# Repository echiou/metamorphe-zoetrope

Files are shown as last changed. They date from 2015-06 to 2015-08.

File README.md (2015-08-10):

# MetaMorphe Zoetrope #
#### By: [Tim Campbell](http://github.com/timcam) and [Ethan Chiou](http://github.com/echiou) ####

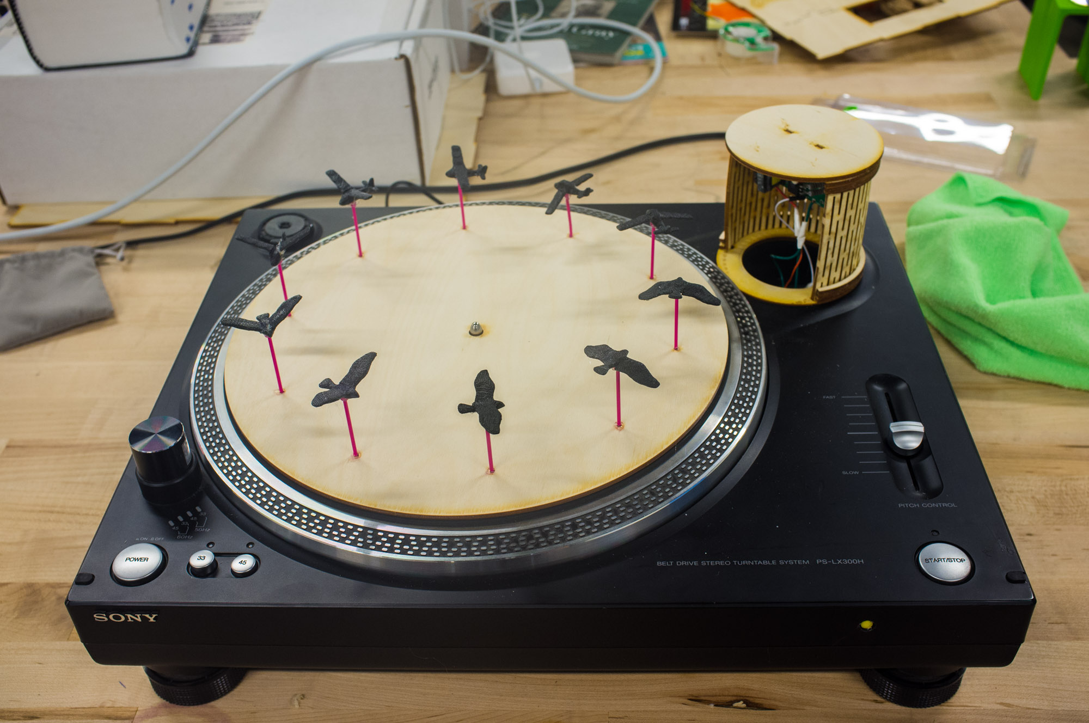
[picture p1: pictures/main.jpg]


A record player modified to demonstrate an application of [Cesar Torres](http://github.com/cearto)' MetaMorphe, namely the ability to interpolate keyframes from a programatically defined change in a 3D model. The record player, which rotates at around three times its built-in speeds (~99 and 135, instead of 33 and 45 rpm, respectively), has either 15 or 10 3D printed models placed on the turntable, and a xenon flash is fired at a corresponding rate to produce the illusion of animation.

A video can be found [here](https://youtu.be/nmKtfB-Ih18).

## How To Run It ##
- Press power button to turn record player on.
- Ensure the strobe off before proceeding
- Select appropriate speed:
    - "33" for 15 frame animations.
    - "45" for 10 frame animations.
- Place an appropriate plate on the turntable.
- Accelerate the turntable using the start/stop button.
    - Ensure the turntable reaches full speed before turning on the strobe.
- Turn on the strobe with the yellow button on the side of the case.
- Tune the speed of the animation with the pitch fader
- When you are done using the zoetrope:
	- Turn off the strobe
	- Turn off the turntable
	- Turn off power

#### Notes ####

- .svg files for [10](./record-10.svg) and [15](./record-15.svg) frame plates can be found in the repository.
- .stl file for the [cog](./stroboscope-cog-rev1.STL) is found in the repository
- .dxf files for the strobe enclosure found in the [strobe-mount](./strobe-mount) folder in the repository
- The turntable must reach full speed before you turn on the strobe because  firing the strobe light and accelerating the turntable simultaneously draws too much power.

## How We Made It ##
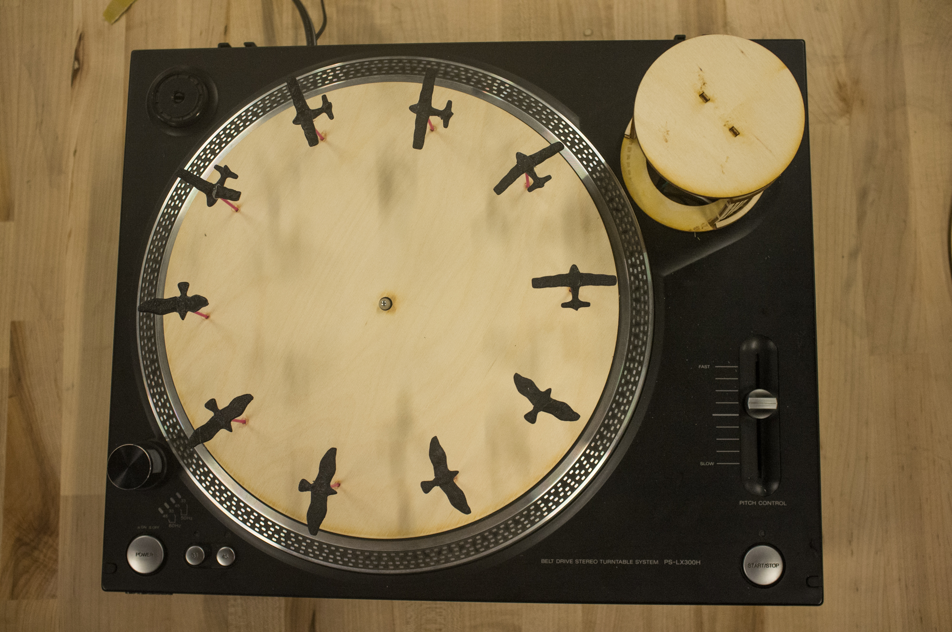
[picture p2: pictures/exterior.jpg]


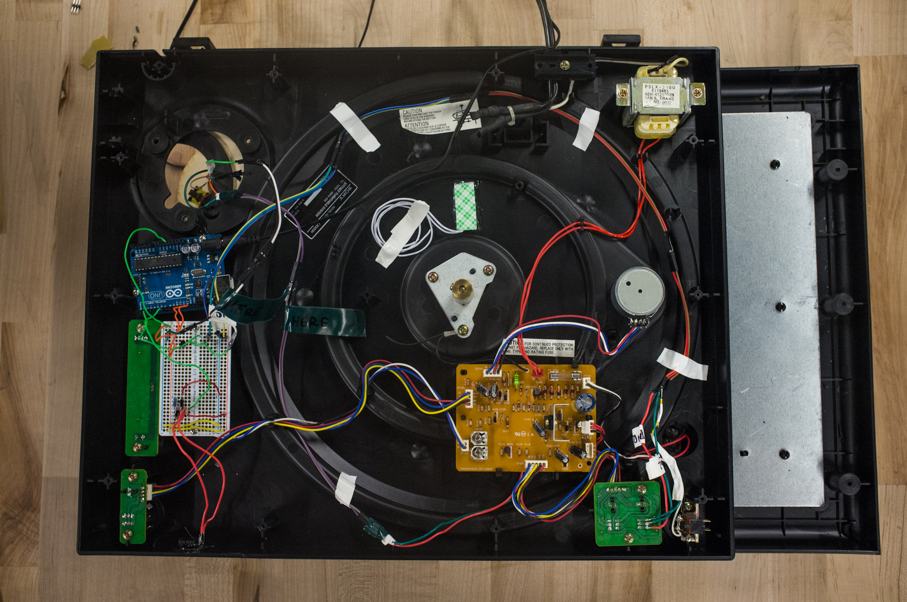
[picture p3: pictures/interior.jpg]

#### 1. [What we started with](#what-we-started-with)
#### 2. [Cog](#cog)
#### 3. [Flash](#flash)
#### 4. [Speed Control](#speed-control)
#### 5. [Circuitry and Programming](#circuitry-and-programming)

## What we started with ##
When approached by Cesar to make a demonstration for MetaMorphe, Tim had the idea of making a zoetrobe or stroboscope to present the potential of MetaMorphe to produce keyframes in animation. We decided on a record player because of the already-implemented rotational motion and the size of the turntable. 
We found an inexpensive, used record player on Craigslist that I picked up in Oakland, and took it apart to see how it worked, and how we could modify it to do what we wanted.

#### Built-In Buttons ####
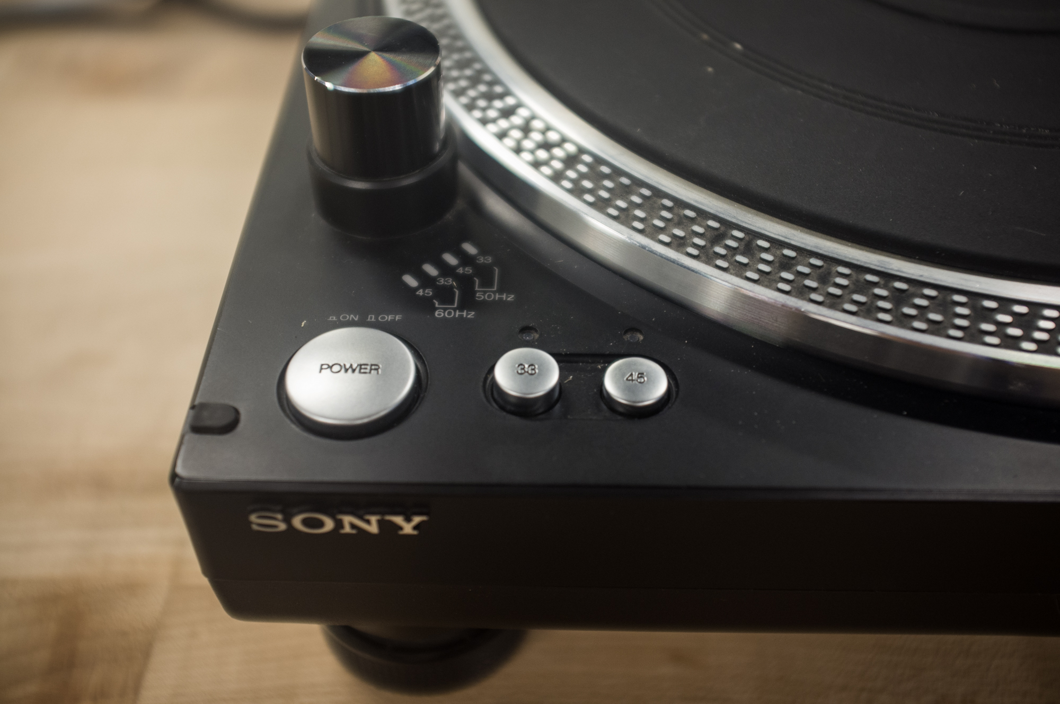
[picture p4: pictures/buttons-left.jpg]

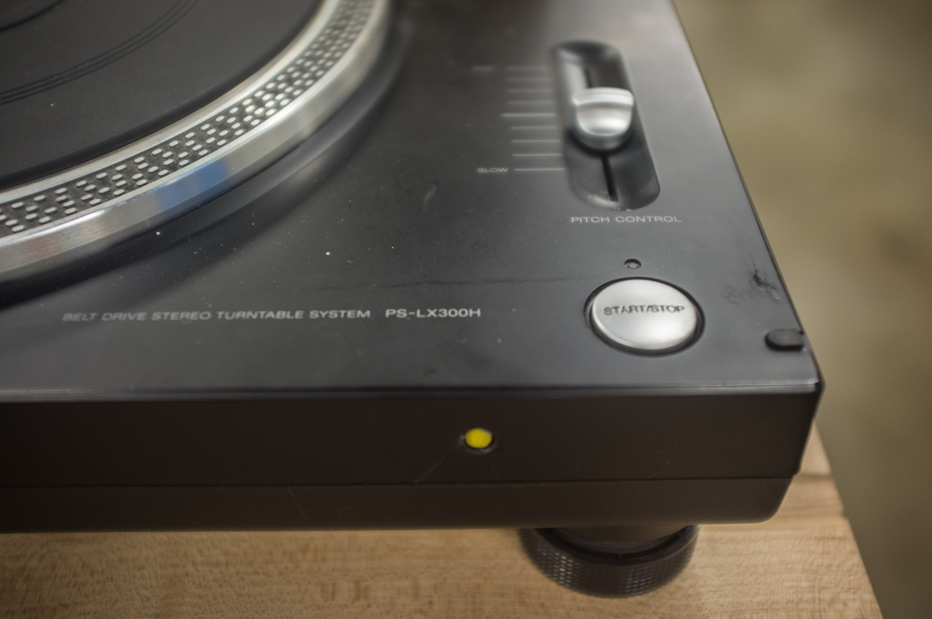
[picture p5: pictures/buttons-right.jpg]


On the left side, there is a power button, as well as options for speed, which were intially at 33 and 45 rpm. We initially wanted to display the animation at around 24 frames per second (fps). With 10 frames of animation, a 45 rpm turntable would display at 7.5 fps. Therefore, we calculated a necessary speed of 144 to 150 rpm for 10 frames at 24 fps. Upon seeing the different speeds, we then calculated the proportioned number of frames for the 33 rpm setting and also implemented a 15 frame plate.
On the right side, there is a start/stop button for the turntable, as well as pitch control, which alters the rotational speed of the turntable slightly. There is also the yellow button I added in to turn the strobe light on and off.

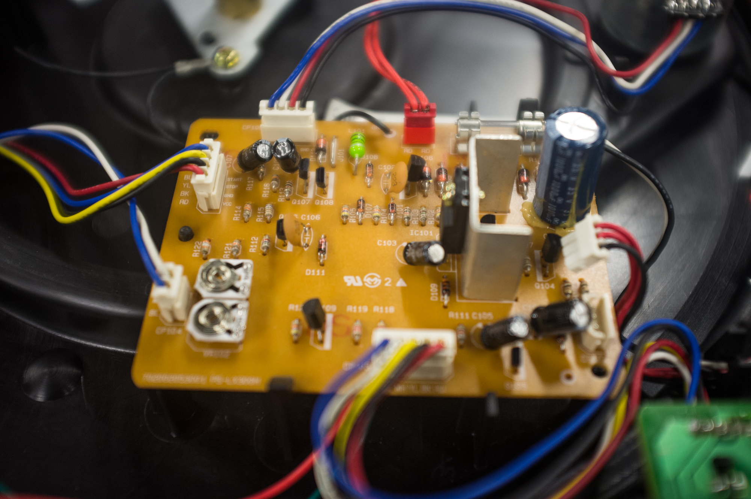
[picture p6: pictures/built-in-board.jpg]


Looking at the internals of the record player, we found an analog circuit board with a 12v regulator, which was coincidental because Tim had a 12v xenon flash on hand, and so we could power the flash without an additional power source. The 12V regulator was speced to handle steady current output of 1A, which we estimated to be enough current to power both the motor and the strobe.

## Cog ##

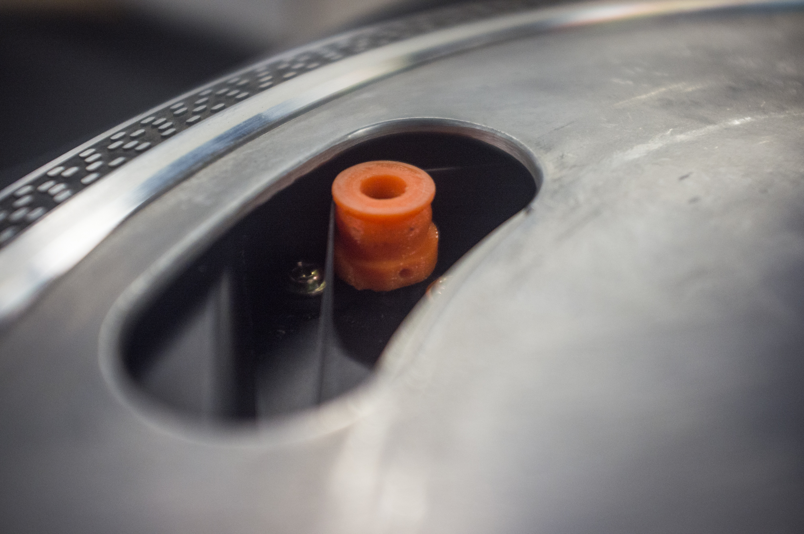
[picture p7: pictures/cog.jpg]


Because we wanted to spin the turntable at three times its default speeds, we decided that instead of replacing the motor, we could simply fit a larger pully over the existing one, which would increase the speed of the larger turntable. Tim measured the diameter of the existing pulley and then tripled its size on the 3D printed retrofit. The Solidworks [file](./stroboscope-cog-rev1.SLDPRT) is in the repository. An good explanation of crowned pulleys can be found on [woodgears.ca](http://woodgears.ca/bandsaw/crowned_pulleys.html)

## Flash ##

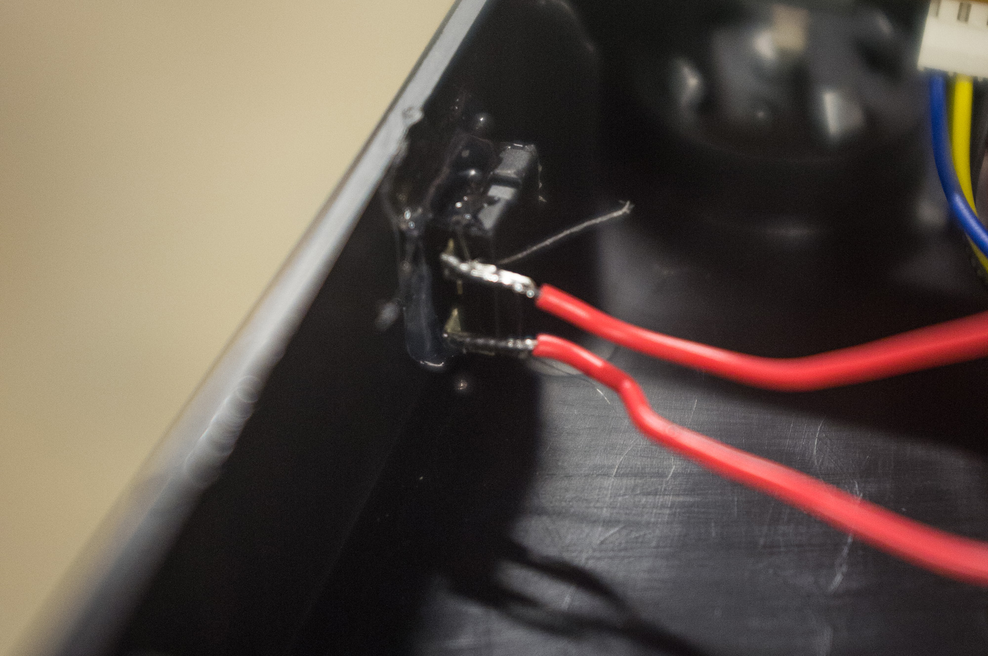
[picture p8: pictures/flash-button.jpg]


Because of the limitations of the record player's power supply, we needed a way to turn the strobe off as the turntable was accelerating. To do this, we simply added a button on the side of the casing connected to the Arduino controlling the flash.

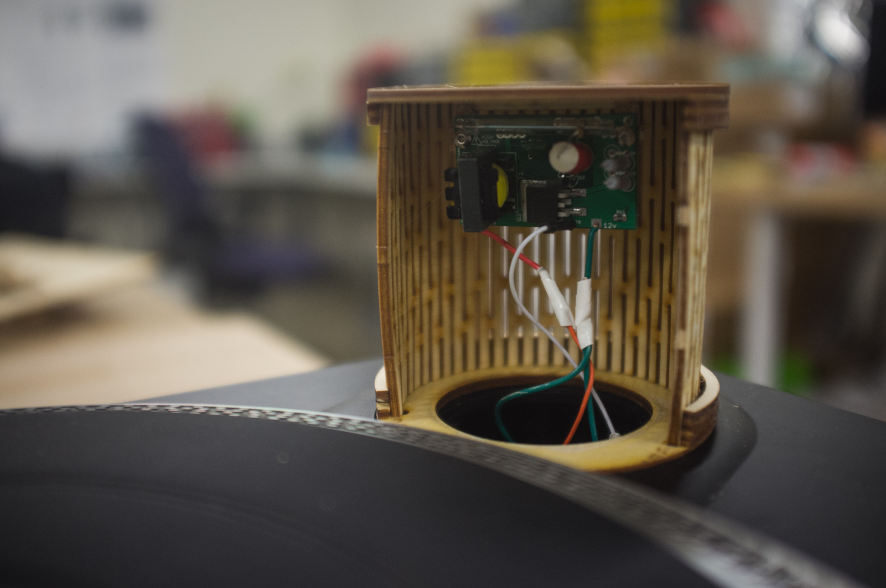
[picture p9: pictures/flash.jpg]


The strobe light is an on-demand power strobe. It charges an 800 V capacitor from a 12 V power supply then discharges from a trigger signal between 5V and 12V. We triggered the stobe with a transistor connected to an Arduino digital output pin. The current draw of the strobe is determined by the triggering frequency, which was approximately 0.4 A for our 24 fps application. Tim had the strobe module lying around from a previous project, it can be purchased as an assembled module from [xenonflashtubes.com](http://www.xenonflashtubes.com/12v-power-strobe.html)

In addition to powering the strobe light with the record player's power supply and controlling it with the Arduino, we had to position it illuminate the animation. We did this by replacing the record player's needle with a laser cut mount for the flash. 

## Speed Control ##

In order to find the speed at which the turntable was spinning (and thus at what rate to fire the strobe light), we initially had the idea of putting a Reed switch and a magnet under the turntable find the rotations per minute (and actually cut a hole in the casing and hot glued the switch in). Then we settled on a elegant solution: instead of adding lots of logic and components, we could use the built-in pitch control to adjust the speed of the turntable ever so slightly while we fired the flash at a constant rate. This required no additional electronics or modification. 

#### Different Built-in Speeds ####

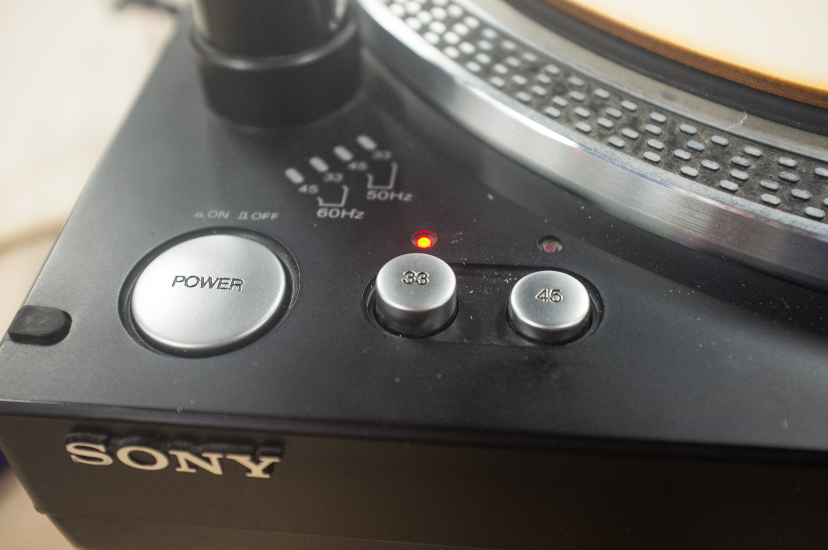
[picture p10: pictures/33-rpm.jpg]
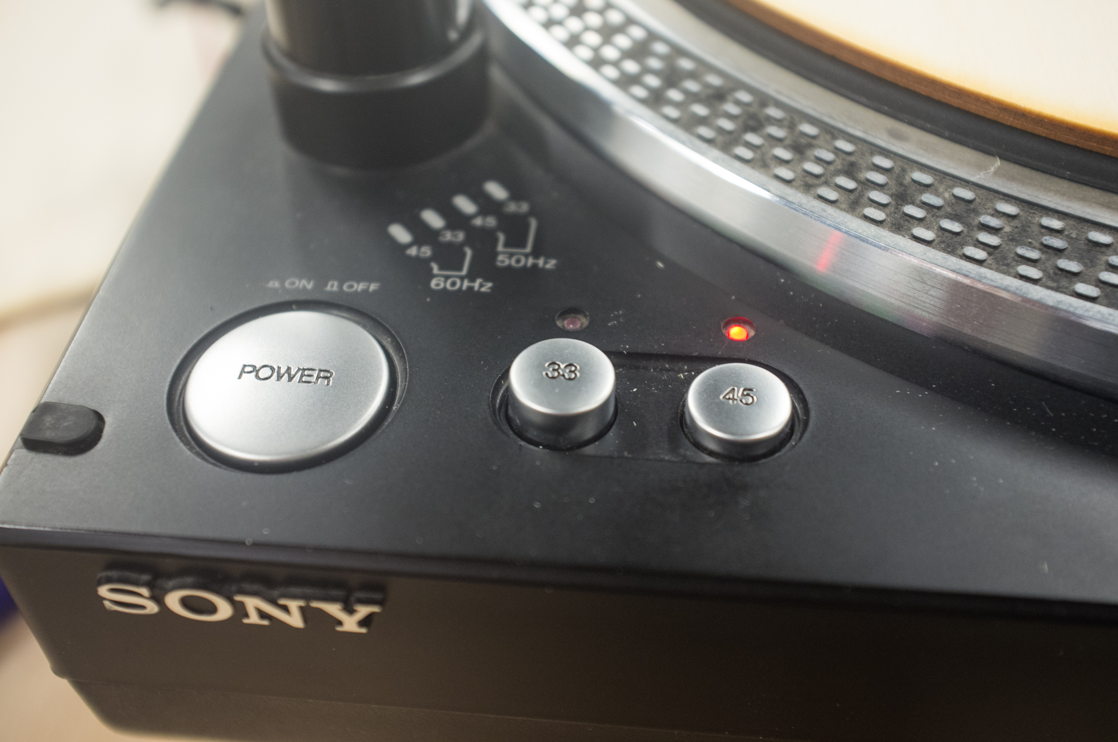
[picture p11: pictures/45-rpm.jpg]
 

The record player also came with two default speeds, the faster of which we used for 10 frame animations (and would thus fire the flash at around 30 fps). We also decided to take advantage of the slower speed and use it for 15 frame animations. To do this, we had to be able to detect at what rate the turntable was spinning.

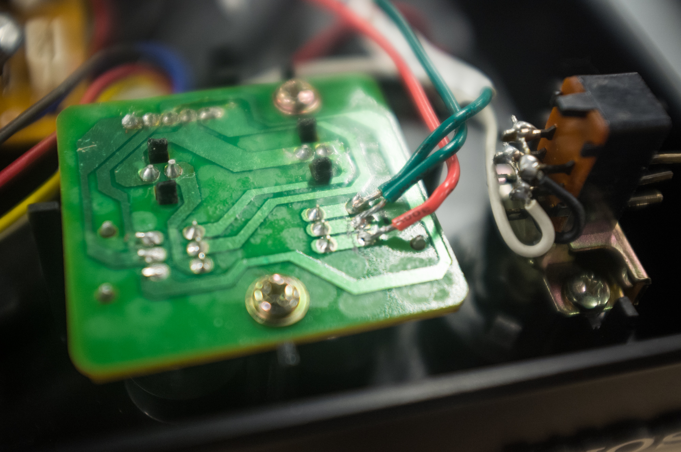
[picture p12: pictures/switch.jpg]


Our intuition was to try to read the voltage from the LEDs indicating at which speed the turntable was turning, but the voltages which we were getting were confusing (and in the process we managed to burn out several LEDs as well as an Arduino). Instead of dealing with the same switch as the record player's circuit board, we chose an unused one, and simply read the signal from there. The unused switch was connected mechanically but not electrically to the other switch, thus saving the confusing voltage. 

## Circuitry and Programming ##

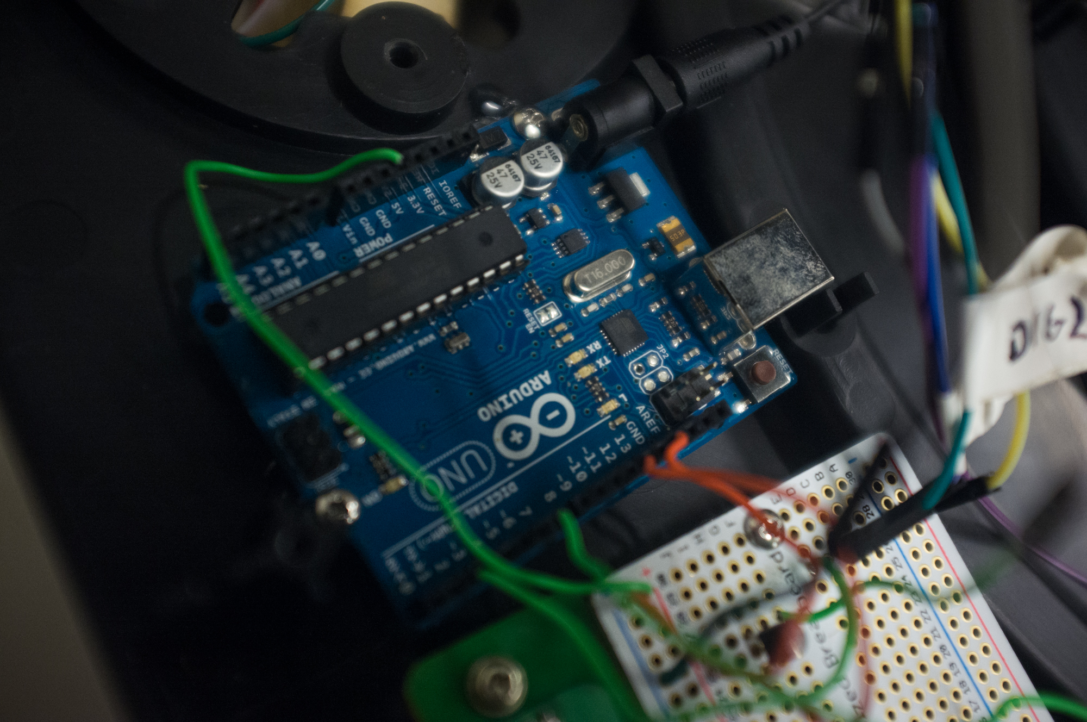
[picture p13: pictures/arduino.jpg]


My Arduino code can be found [here](./MetaMorpheZoetrope/MetaMorpheZoetrope.ino). It essentially fires the flash at a constant delay if the on/off button is pressed, changing the delay depending on the current speed of the turntable. We initially thought there would be much more programming involved but the record player had so much existing functionality that only timing the strobe was necessary. 

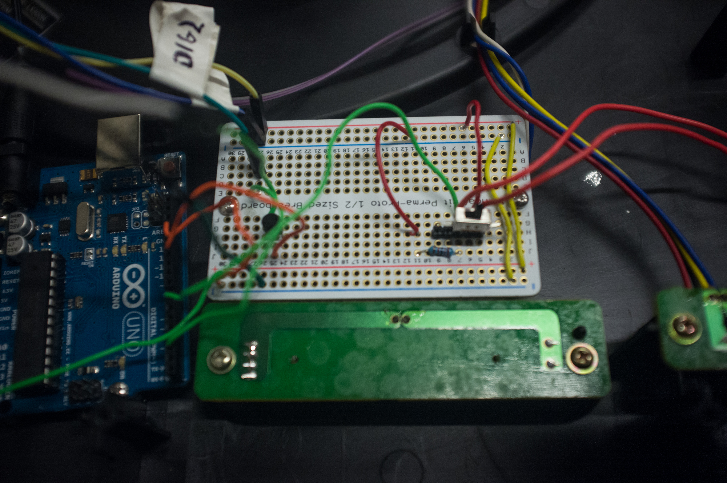
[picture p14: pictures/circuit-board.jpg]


The perma-proto board contains wires to the arduino, as well as wires to the switch detecting the current turntable speed, the button to turn the strobe on and off, and the strobe itself. There is also a switch connected to it that we used to turn the strobe on and off before putting the button in. We hot-glued stand-offs to the underside of the top case and then screwed the Arduino and protoboard into them. 

[main]: ./pictures/main.jpg
[exterior]: ./pictures/exterior.jpg "The exterior of the final result."
[interior]: ./pictures/interior.jpg "The interior of the final result."
[left]: ./pictures/buttons-left.jpg "Buttons on left side."
[right]: ./pictures/buttons-right.jpg "Buttons on right side."
[built in]: ./pictures/built-in-board.jpg "The analog circuitboard that came with the record player."
[cog]: ./pictures/cog.jpg "The 3D printed cog."
[flash]: ./pictures/flash.jpg "The flash with its laser cut case."
[flash button]: ./pictures/flash-button.jpg "Wiring for the button to turn flash on and off."
[33 rpm]: ./pictures/33-rpm.jpg "Turntable running at "33 rpm""
[45 rpm]: ./pictures/45-rpm.jpg "Turntable running at "45 rpm""
[33 switch]: ./pictures/switch.jpg "Wiring to read the current speed of the turntable"
[arduino]: ./pictures/arduino.jpg "The Arduino"
[circuit board]: ./pictures/circuit-board.jpg "The circuit board"

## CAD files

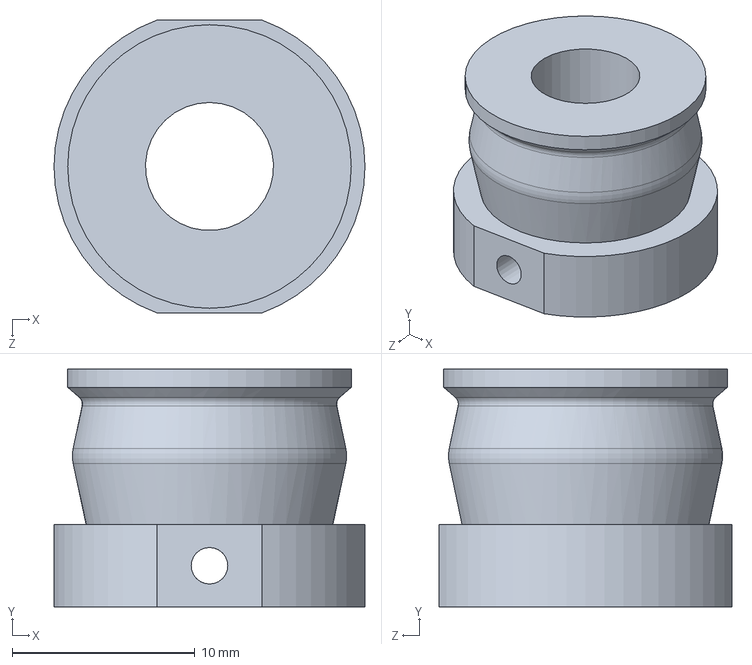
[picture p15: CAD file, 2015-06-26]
stroboscope-cog-rev1.SLDPRT
17.0 x 13.0 x 16.0 mm

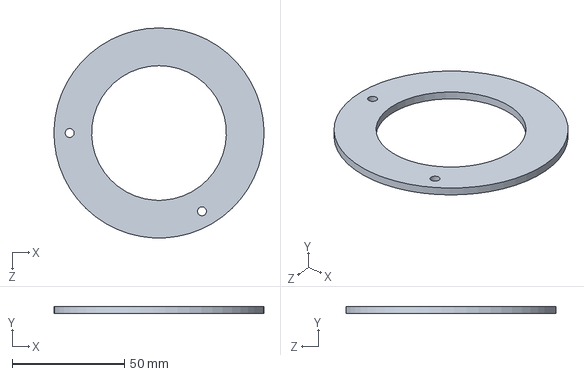
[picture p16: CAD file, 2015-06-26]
strobe-mount/stroboscope-bottompiece-rev1.SLDPRT
93.6 x 3.17 x 93.6 mm

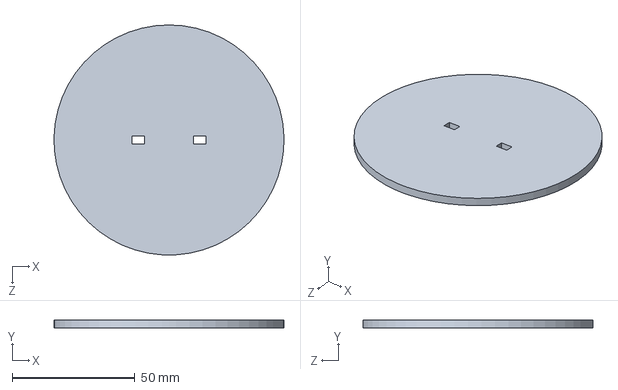
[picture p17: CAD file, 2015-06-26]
strobe-mount/stroboscope-toppiece-rev1.SLDPRT
93.6 x 3.17 x 93.6 mm

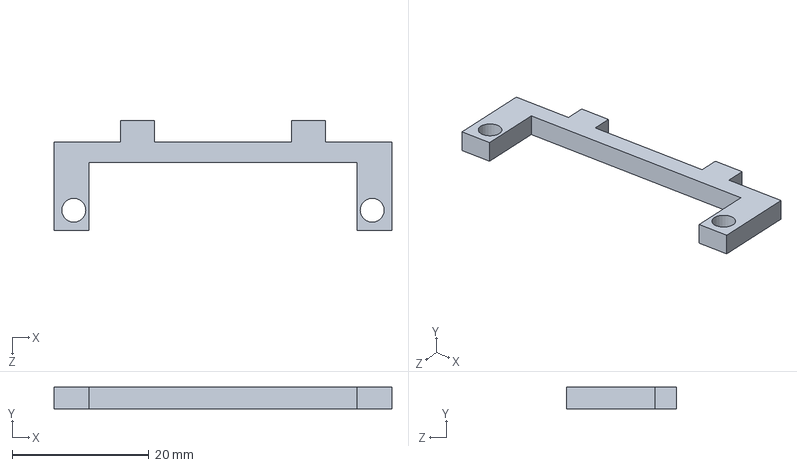
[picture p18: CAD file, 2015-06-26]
strobe-mount/stroboscope-circuitboard-holder-rev1.SLDPRT
49.5 x 3.17 x 16.2 mm

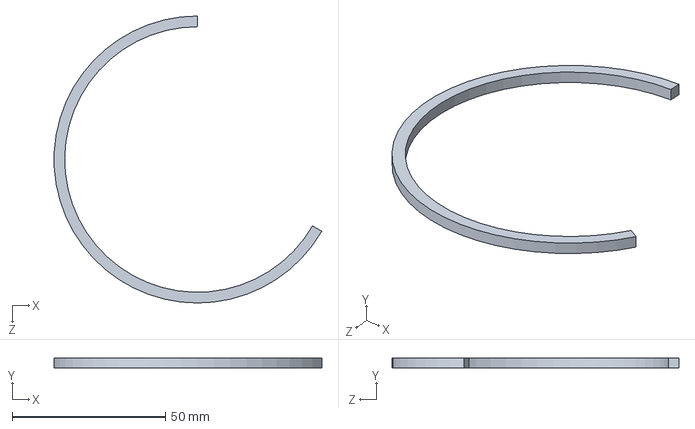
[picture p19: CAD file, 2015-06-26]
strobe-mount/stroboscope-ring-rev1.SLDPRT
87.3 x 3.17 x 93.6 mm

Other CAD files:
strobe-mount/stroboscope-holder-rev1.SLDPRT
strobe-mount/stroboscope-bottompiece-rev1.DXF
strobe-mount/stroboscope-circuitboard-holder-rev1.DXF
strobe-mount/stroboscope-ring-rev1.DXF
strobe-mount/stroboscope-toppiece-rev1.DXF
stroboscope-cog-rev1.STL

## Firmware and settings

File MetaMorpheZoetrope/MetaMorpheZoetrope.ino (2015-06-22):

/*
  MetaMorphe Zoetrope
  Controls the strobe light for a modified turntable to act as a zoetrope/stroboscope.
  Can accomodate 10 and 15 frame "records".
 */

const int switch33 = 2; // Pin number to detect if running at "33 rpm" (15 frames)
const int lightSwitch = 7; // Pin num of the button to turn strobe on and off
const int strobe = 12; // Pin number of the strobe

int lightOn; // Whether or not strobe is on
boolean fifteenFrames = false; // Whether or not we are using 15 or 10 frames
int delayTime = 37; // Delay between strobe flashes

void setup() {
  pinMode(switch33, INPUT);
  pinMode(lightSwitch, INPUT);
  pinMode(strobe, OUTPUT);
}

void loop() {
  // Running at 15 frames but it hasn't been set:
  if (!fifteenFrames && digitalRead(switch33) == 1) {
    fifteenFrames = true;
    delayTime = 35;
  }
  // Running at 10 frames but it hasn't been set:
  else if (fifteenFrames && digitalRead(switch33) == 0) {
    fifteenFrames = false;
    delayTime = 37;
  }

  // Read the state of the switch
  lightOn = digitalRead(lightSwitch);

  // If switch on, lightOn is HIGH:
  if (lightOn == HIGH) {
    // Flash strobe
    digitalWrite(strobe, HIGH);
    delay(1); // Wait for a millisecond
    digitalWrite(strobe, LOW);
  }

  delay(delayTime); // Wait proper amount of time before flashing again
}

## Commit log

2015-06-20 Switch out some pictures, put images in readme, add how to run and ToC to readme.
2015-06-26 added strobe mount and cog files
    [stroboscope-bottompiece-rev1.DXF, stroboscope-bottompiece-rev1.SLDPRT, stroboscope-circuitboard-holder-rev1.DXF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]
